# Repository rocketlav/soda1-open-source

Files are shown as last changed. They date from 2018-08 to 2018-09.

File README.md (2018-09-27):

# SODA1 Open source rocket project
SODA1 открытый проект одноступенчатой экспериментальной ракеты для вывода атмосферного зонда CanSat в рамках чемпионата RosCanSat 2018. Проект разработан участниками студенческого конструкторского бюро "RocketLAV" Самарского университета, занявших первое место на этом чемпионате. Здесь мы собрали всю документацию, включая чертежи, которые разрабатывали и использовали во время создания данной экспериментальной ракеты. Мы хотим поделиться со всеми желающими и интересующимися нашими знаниями и опытом, надеемся, что вы сможете использовать наши результаты для изучения программирования, электроники и механики. 
***

rocket
rocket

***

Проектные файлы хранятся в четырех папках:
1. В папке Documentation содержится PDF файл с подробным описанием проекта;
2. В папке Electrical разводка платы электроники и ее принципиальная схема, а также исходник для altium designer;
3. В папке Mechanical содержатся чертежи, 3D модели в формате STL и исходники 3D модели Kompas v17;
4. В папке Software содержатся исходный код для платы электроники и алгоритм ее работы.

***

Для того, чтобы скачать весь проект, нажмите на зеленую кнопку "Clone or download" и выберите "Download ZIP".

Если у вас возникли вопросы в процессе работы или у вас есть для нас предложение, пожалуйста, напишите нам на почту: rocketlav.team@gmail.com

или используйте сообщения нашей группы https://vk.com/rocketlav.

# English version

SODA1 is open source project of experimental single stage rocket which is designed to deliver CanSat during Russian CanSat competition 2018. This project was designed by members of student design association "RocketLAV", which won the first prize of this competition. Our team collect all documentation here which we developed and used during rocket's creation. We want to share our knowledge and experience for those who want and interested in it, we hope that you can use our documentation to get learned in software, electronics and mechanical engineering. 

***

Project documentation are placed in four folders:
1. Main PDF file which describes project in detail is placed in Documentation folder, please, be attention, this file fully in Russian;
2. PCB files of electrical board and its principal scheme are placed in Electrical folder; 
3. Mechanical folder contains drawings and 3D model of rocket in stl format and Kompas v17;
4. Software folders contains a source code and algorithms for electrical board of rocket.

***

Mostly this project in russian, but if you need help to translate, feel free to contact us.
If you have any questions about our project or you have an offer for us, please, write to us on email rocketlav.team@gmail.com.

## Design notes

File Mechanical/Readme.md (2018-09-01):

# Описание файлов
Здесь содержатся чертежи в папке Drawings, по которым вы можете изготовить модель ракеты. 

В папке 3D Model содержатся исходники модели и ее сборка, выполенная в среде Компас v17. Также в папках Head Fairings V1 и Head Fairings V2 содержатся 3д модели вариантов механизма открытия головного обтекателя. 

Файлы В разрезе.stl и Без разреза.stl 3д модель ракеты соответственно в разрезе и без разреза в формате STL.

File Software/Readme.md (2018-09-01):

# Описание файлов

EOS_code.ino исходные код для платы бортовой системы. Пины актуальны для разведенной платы, представленной в папке Electrical. 
Если вы собираетесь использовать протокол i2c для подключения барометра, пожалуйста, проверьте адресс устройства через i2c scan. Скетч i2c scan вы можете найти на оффициальном сайте arduino. Полученный адрес вашего устройства необходимо добавить в библиотеку <Adafruit_BMP280.h> для правильной работы барометра.

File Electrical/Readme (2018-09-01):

Описание файлов:

Onboard+Plate+ver1 (altium designer.).pcbdoc исходник платы в altium designer.

PCB Lower Layer.pdf и PCB Upper Layer.pdf разводка платы для ее изготовления методом ЛУТ. PCB_Onboard-Plate.pdf - изображение разводки платы со всеми слоями. Schematic_SODA1_OnBoardElectricalSystem.pdf - принципиальная электроическая схема. 

Это наш первый опыт в разработке и создании плат, по этому мы рекомендуем развести эту плату самостоятельно. Так как плата двухсторонняя, компоненты платы размещается так, чтобы было удобно их паять.

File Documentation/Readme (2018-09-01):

SODA1_Project_Documentation.pdf файл с подробным описанием проекта. В нем содержатся технические подробности, обоснования принятых решений, а также расчеты, которые проводились во время создания проекта.

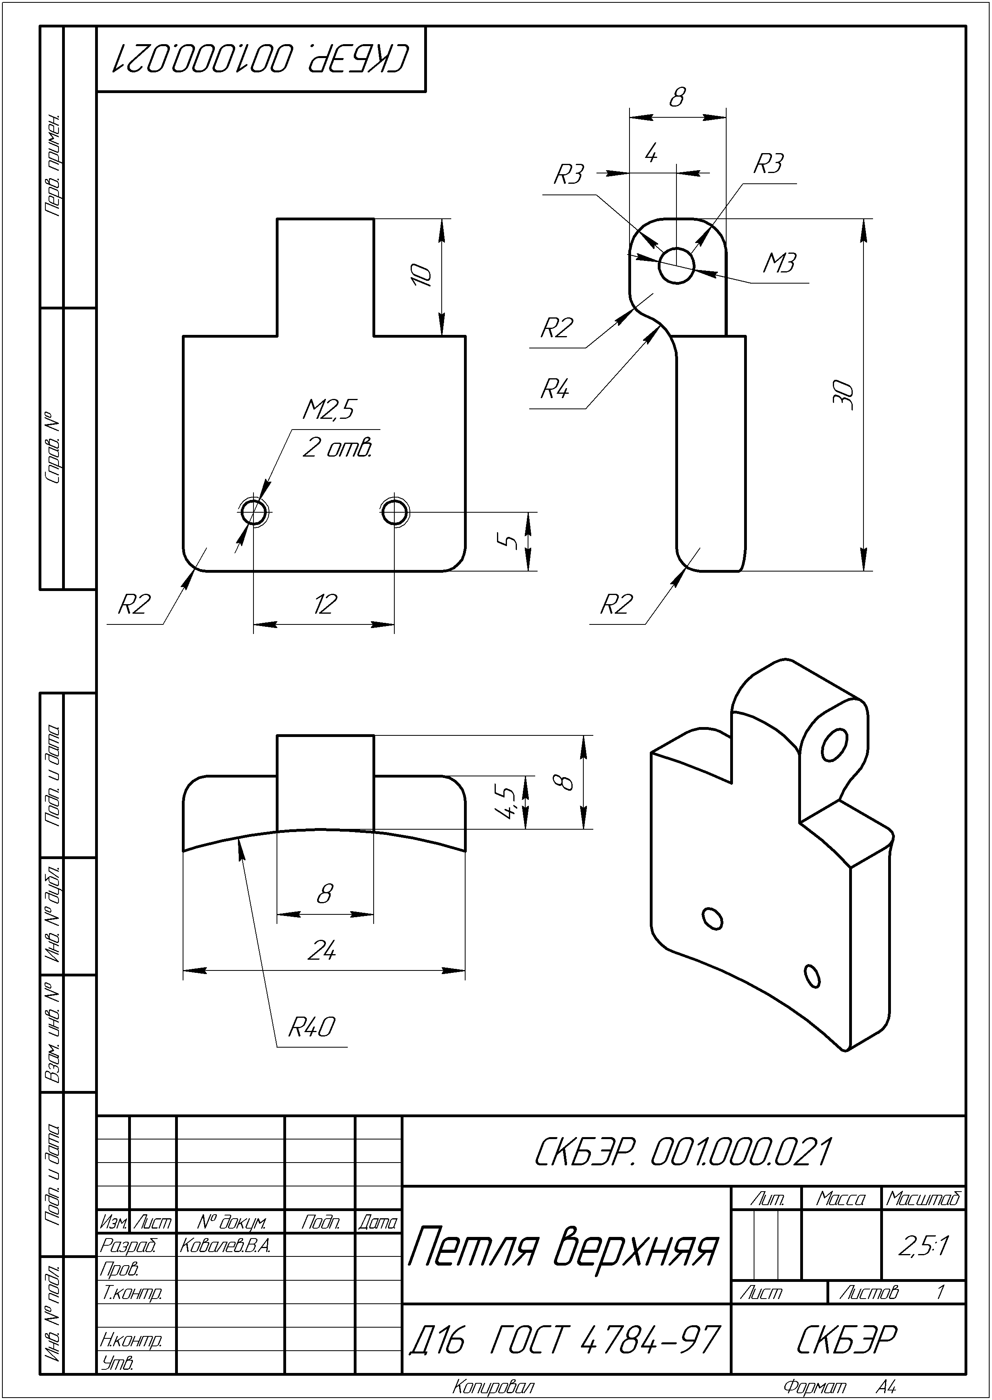
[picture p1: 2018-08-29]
Mechanical/Drawings/21Петля верхняя.png

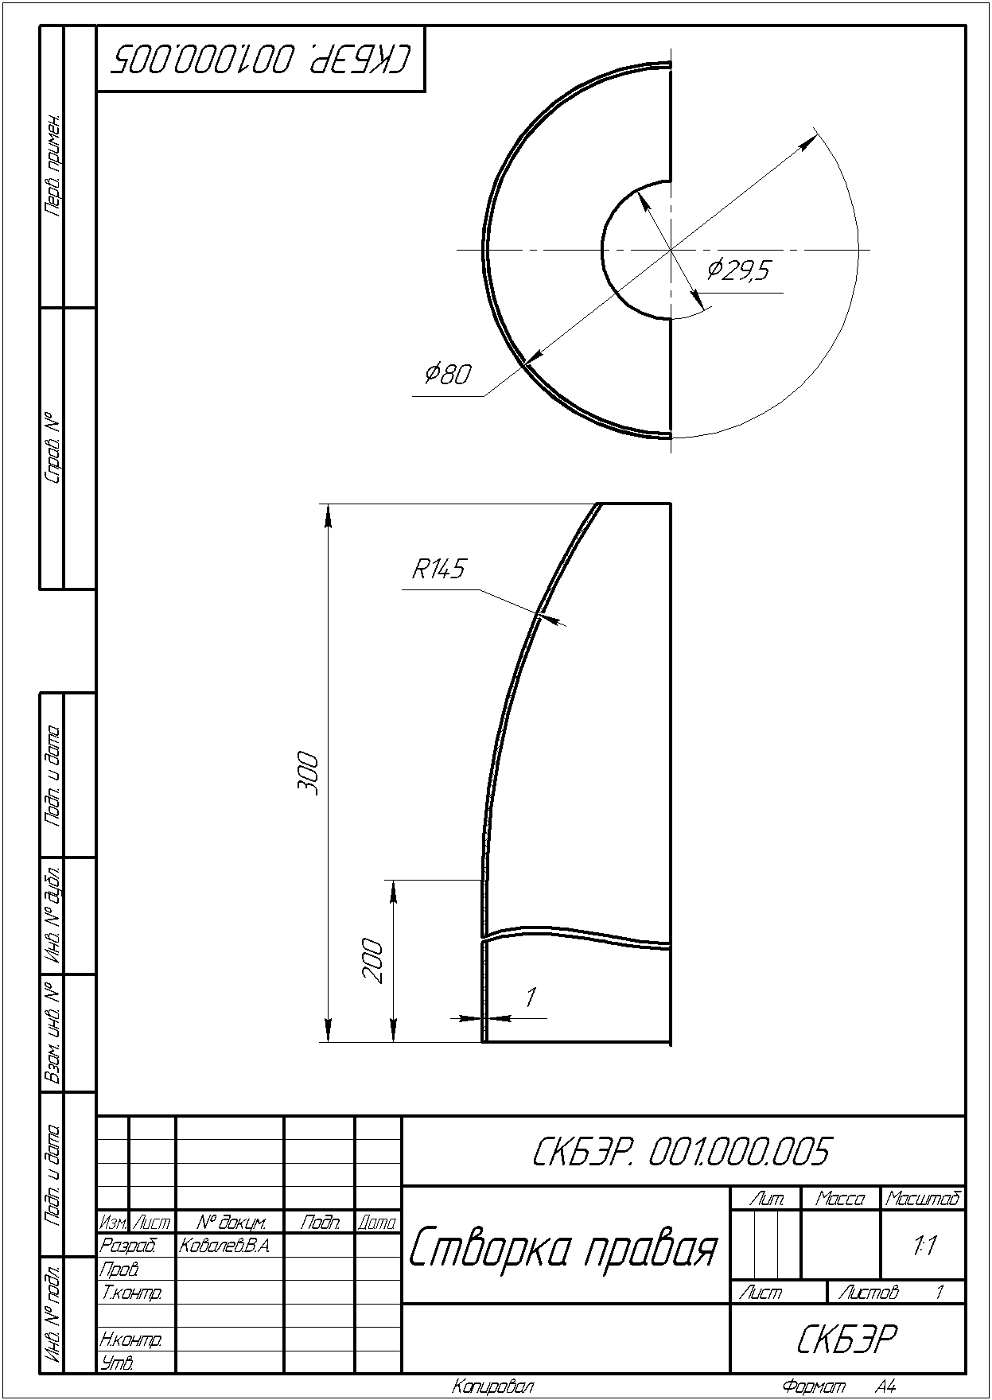
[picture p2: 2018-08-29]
Mechanical/Drawings/5Створка правая.png

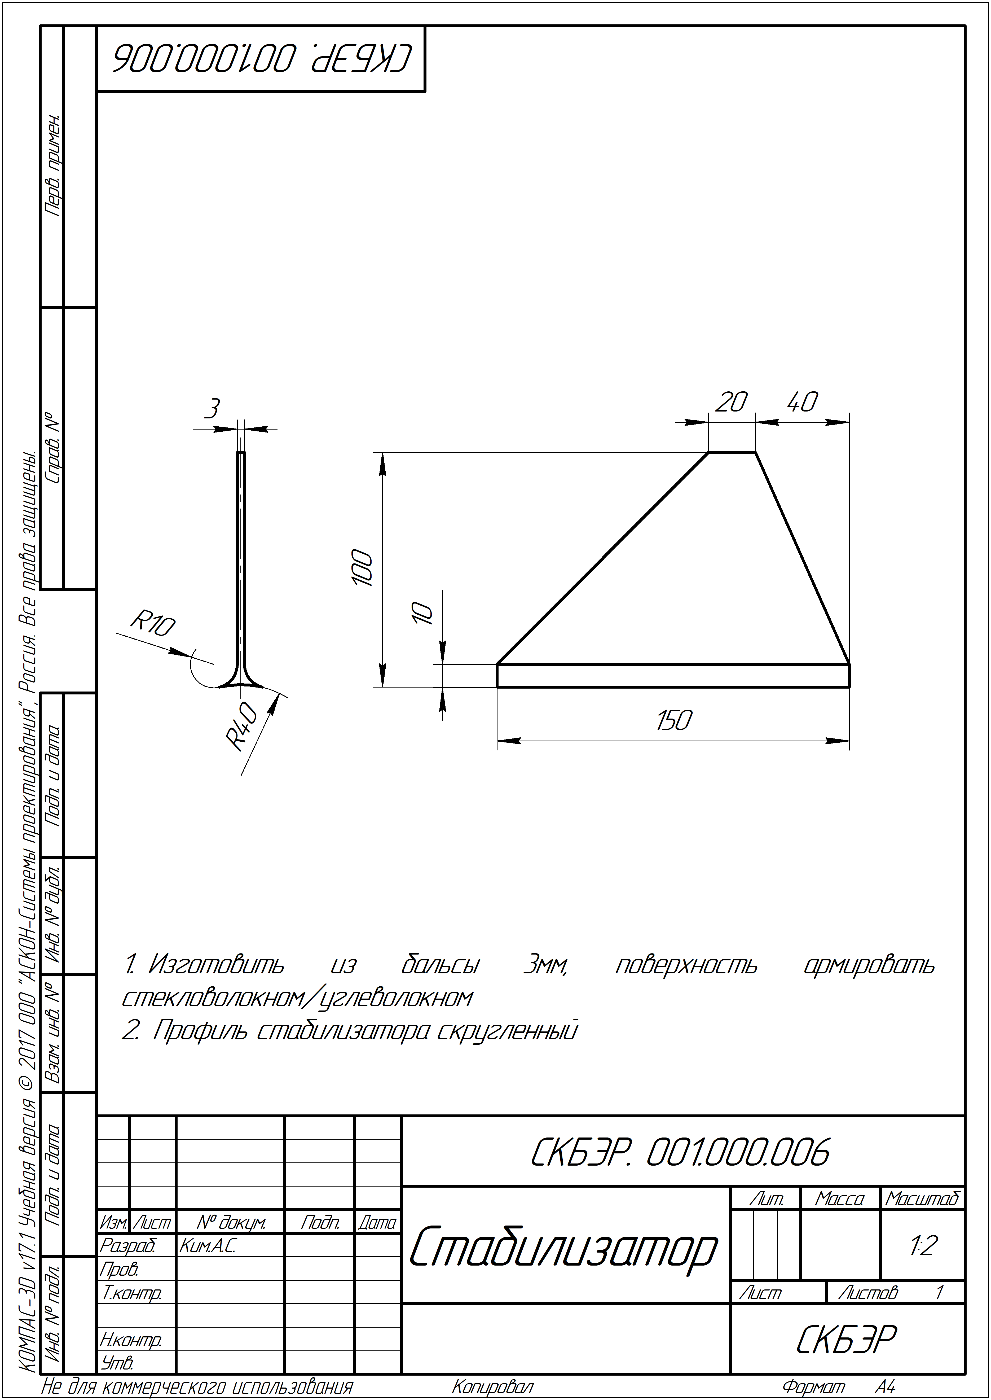
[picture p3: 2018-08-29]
Mechanical/Drawings/6Стабилизатор .png

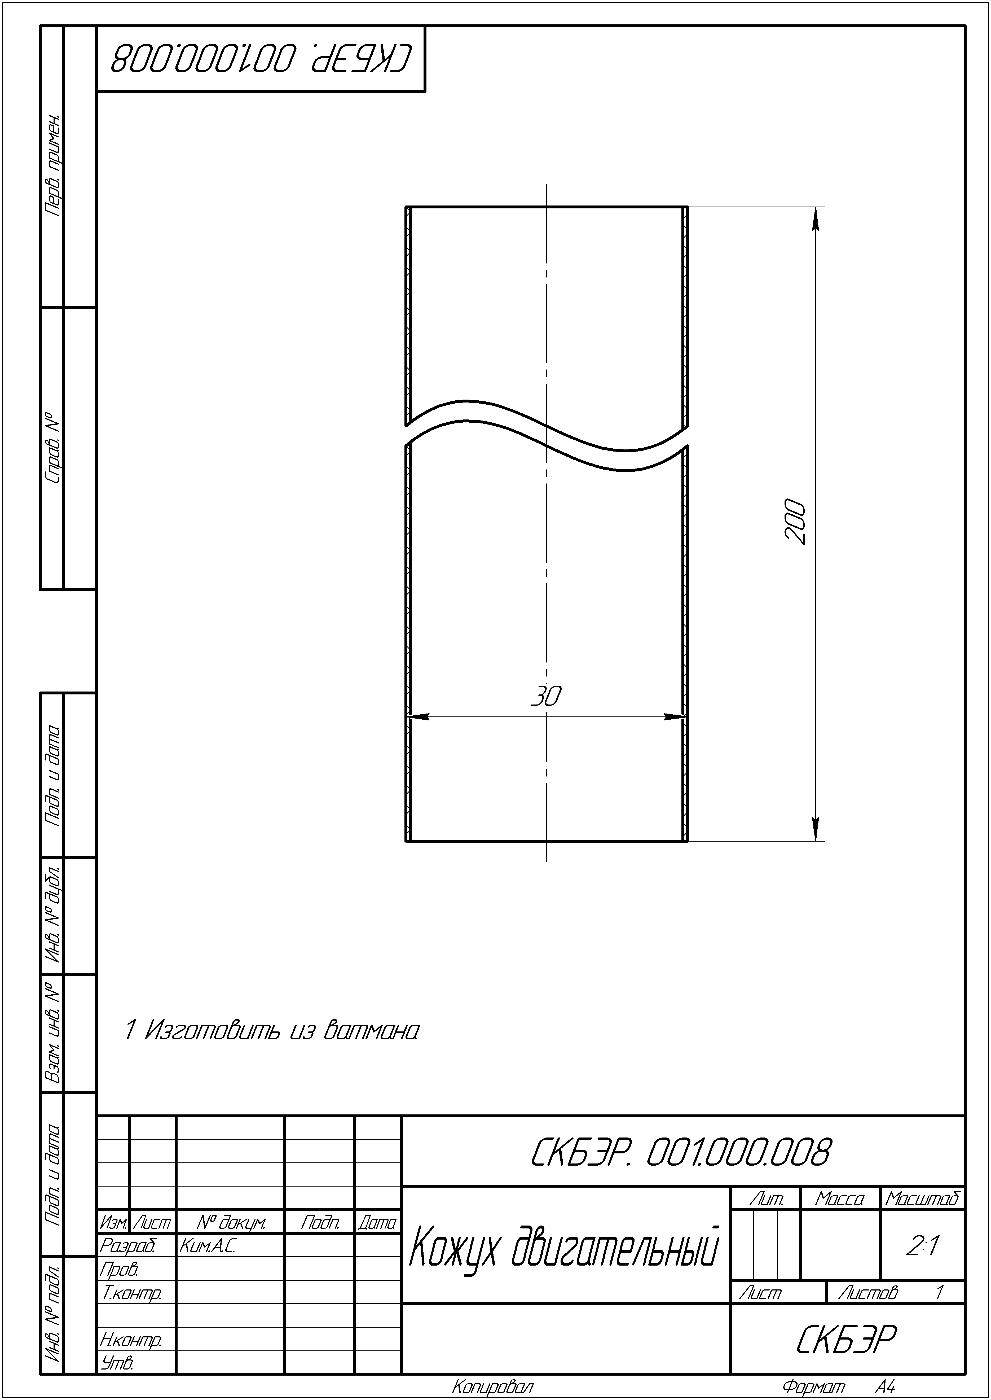
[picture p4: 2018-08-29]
Mechanical/Drawings/8Кожух двигательный.png

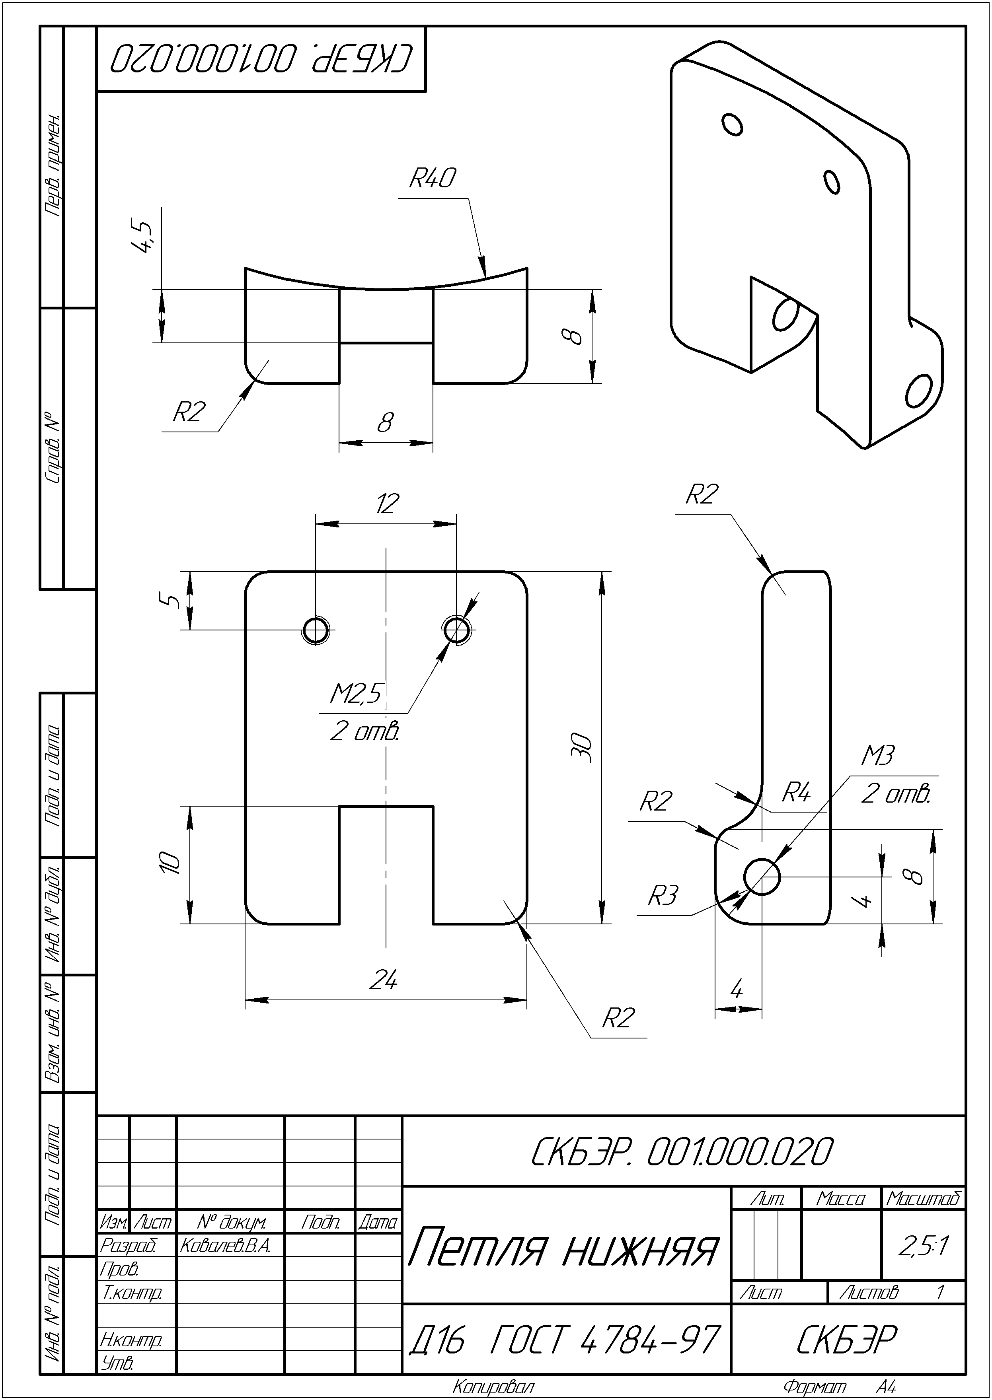
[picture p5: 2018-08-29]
Mechanical/Drawings/20Петля нижния.png

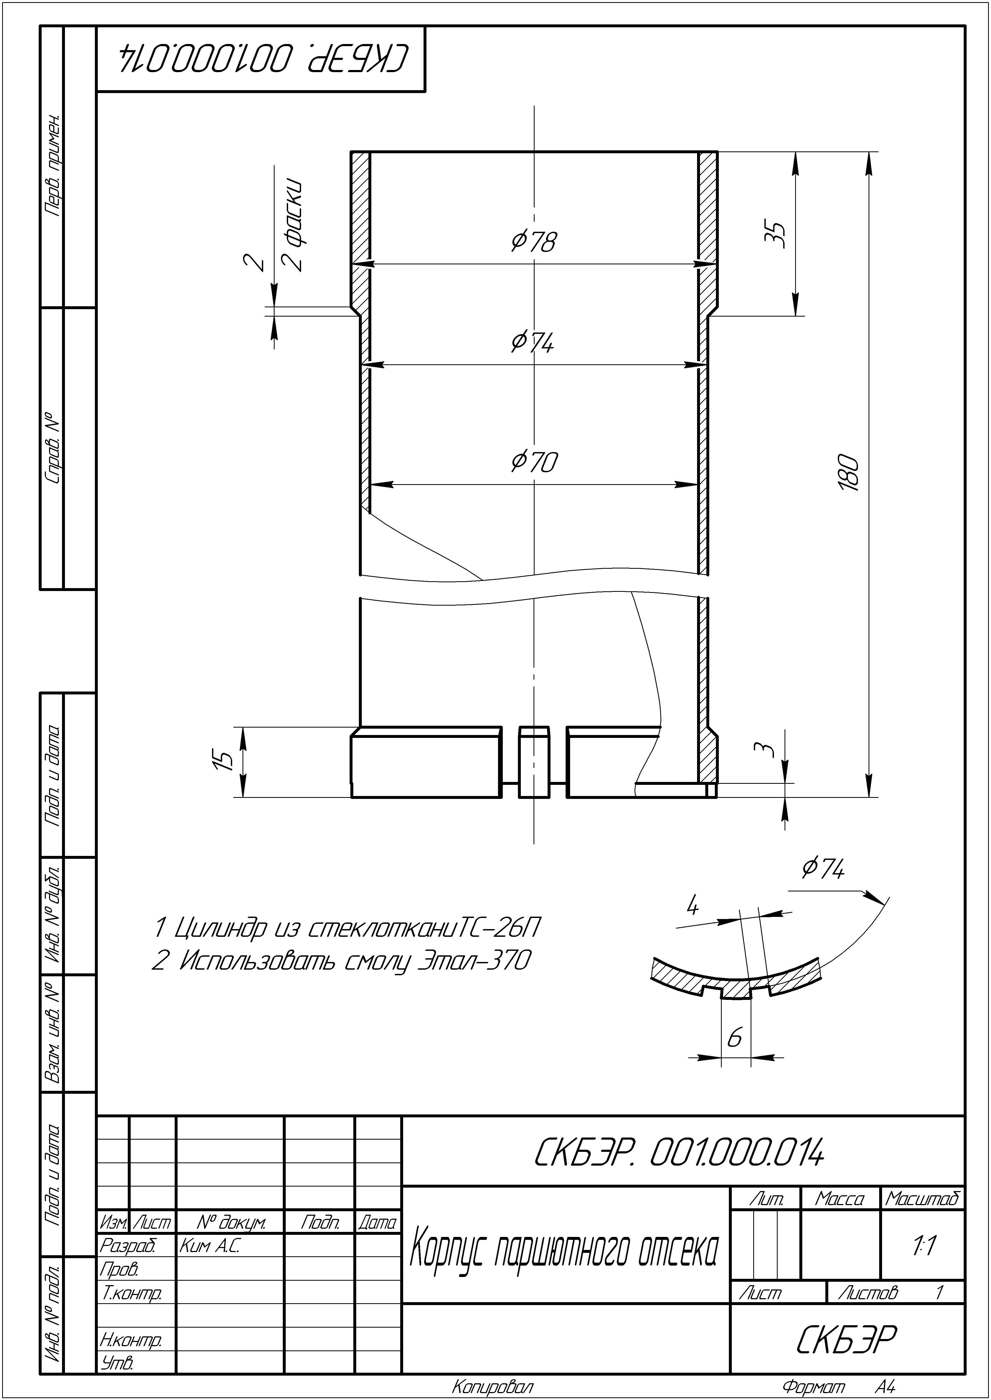
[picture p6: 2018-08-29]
Mechanical/Drawings/14Корпус парашютного отсека.png

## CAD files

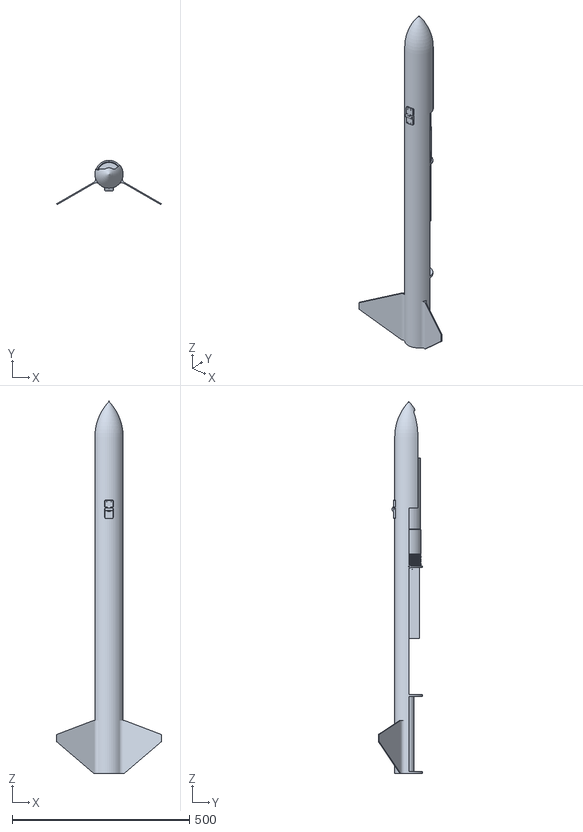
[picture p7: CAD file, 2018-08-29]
Mechanical/В разрезе.stl
295.9 x 125.3 x 1050.0

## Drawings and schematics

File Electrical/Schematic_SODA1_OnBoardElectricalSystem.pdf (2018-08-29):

## Power supply

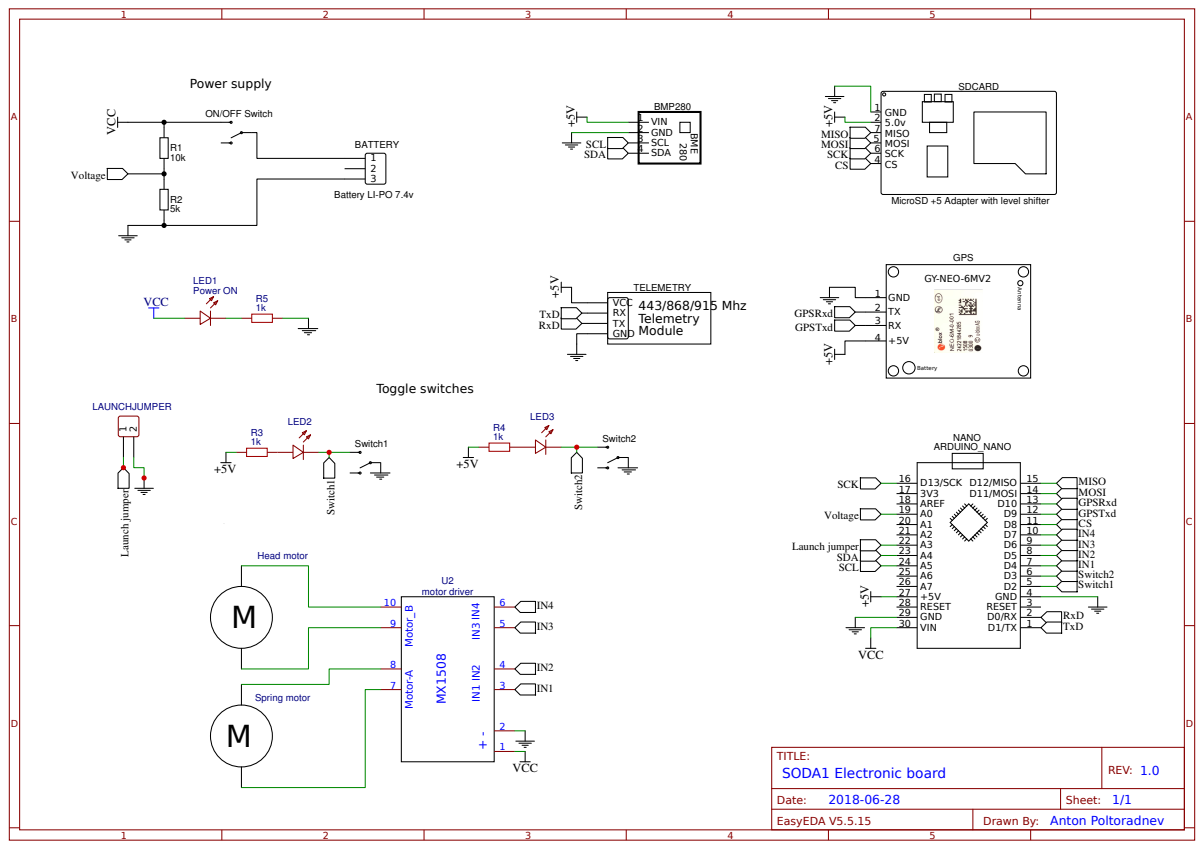
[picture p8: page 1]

MicroSD +5 Adapter with level shifter

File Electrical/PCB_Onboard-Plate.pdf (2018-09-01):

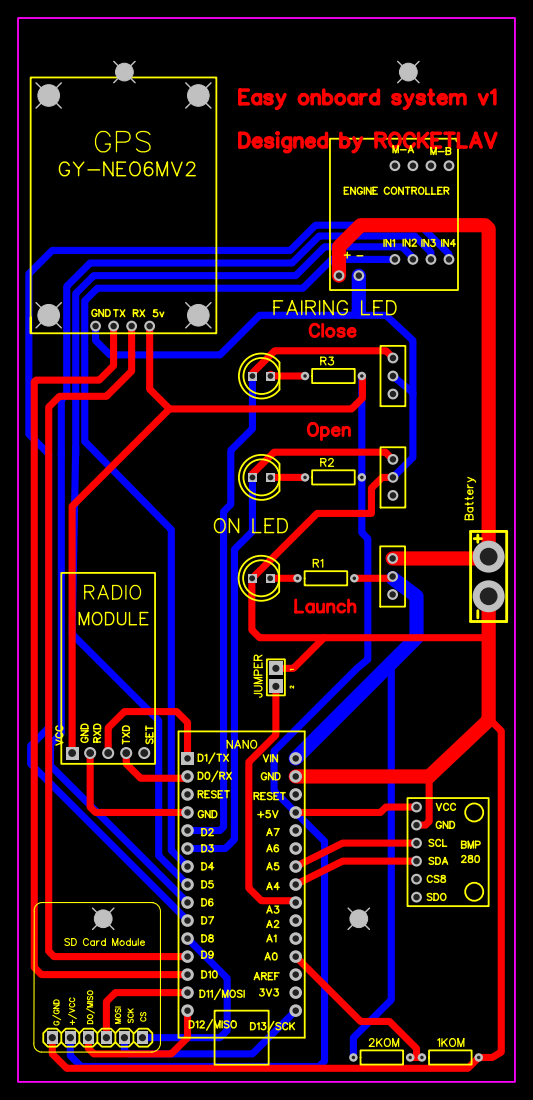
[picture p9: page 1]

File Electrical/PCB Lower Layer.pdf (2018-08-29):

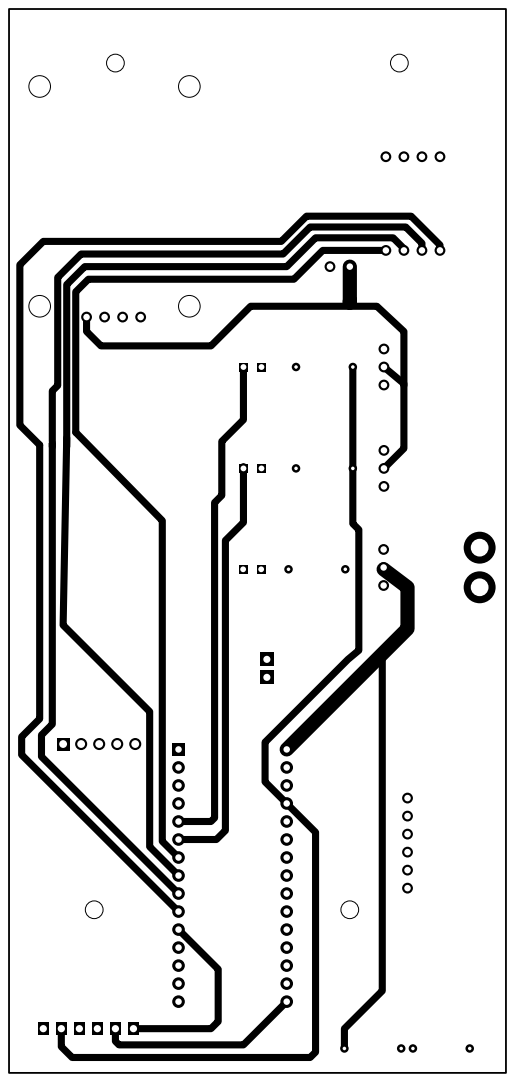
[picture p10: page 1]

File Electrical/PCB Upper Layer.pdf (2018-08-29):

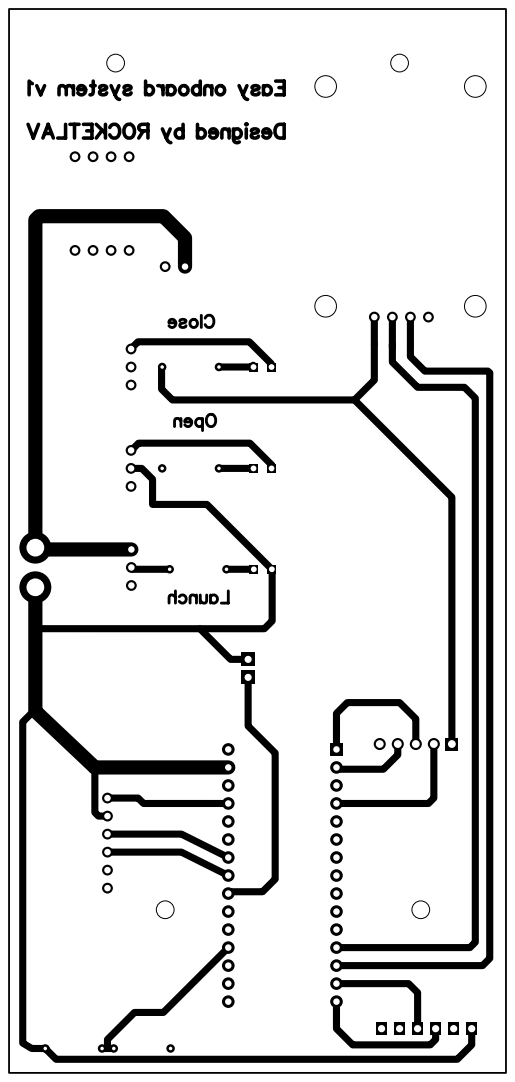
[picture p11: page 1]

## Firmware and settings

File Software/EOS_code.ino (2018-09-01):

#include <Adafruit_BMP280.h> // Изменить в этой бибилотеке адрес устройства на 0x76
#include <SoftwareSerial.h>
#include <SD.h>

/// Контактные пины, не трогать, в плате они фиксированные
SoftwareSerial GPS(9, 10); //Инициализация GPS по программному сериалу RX, TX
Adafruit_BMP280 BMP;   //Инициализация барометра
const int chipSelect = 8; //Тоже фиксированный пин на плате
File dataFile;

// ПЕРЕМЕННЫЕ

unsigned long DelayForBMP = 125; // Время опроса барометра
unsigned long BufferForBMP = 0;

unsigned long DelayForSD = 10000; // Время сохранения данных на сд
unsigned long BufferForSD = 0;

float BMSKoef = 0.01346; //Коэффициент для определения напряжение на аккумуляторе, для вашего аккума нужно рассчитать самостоятельно

unsigned long StartTime = 0;
unsigned long SaveTimer = 5500; // Время раскрытия после отрыва
unsigned long SaveEndTime = 1500; // Время работы двигателя системы открытия
unsigned long EndBuffer = 0;

unsigned long Save2Timer = 1000; // + SaveTimer система спасения
unsigned long Save2EndTime = 1500; // Время работы двигателя системы открытия
unsigned long End2Buffer = 0;

bool StartDrive = false;
bool Start2Drive = false;

void setup()
{
  pinMode(A0, INPUT); // VCC VOlTAGE
  pinMode(A3, INPUT_PULLUP); // jumper
  pinMode(3, INPUT); // пружина (Верхний)
  pinMode(2, INPUT); // голова (Нижний)
  // motor
  pinMode(4, OUTPUT); // Пружина
  pinMode(5, OUTPUT);

  pinMode(6, OUTPUT); // Голова
  pinMode(7, OUTPUT);

  // Инициализация всех портов
  Serial.begin(9600); // БОД радио модуля
  while (!Serial) {
    // wait for serial port to connect. Needed for native USB port only
  }

  GPS.begin(9600);

  if (!BMP.begin()) {  //Подключаем барометр
    Serial.println("BMP NOT FOUND");
  }
  else Serial.println("BMP IS OK");

  if (!SD.begin(chipSelect)) {
    Serial.println("Card failed, or not present");
  }
  else Serial.println("CARD IS OK");

  dataFile = SD.open("datalog.txt", FILE_WRITE);

  float voltage = analogRead(A0) * BMSKoef;
  Serial.println("Voltage: " + String(voltage));
  dataFile.println("Voltage: " + String(voltage));

  Serial.println("GPS value: ");
  // GPS tester
  bool gpsTester = false;
  while (!gpsTester) {
    while (GPS.available()) {
      char a = GPS.read();
      Serial.write(a); // Вывод в радио
      gpsTester = true;
    }
  }

  Serial.println("");
  Serial.println("INIT END");

  bool isReady = false;
  int headValue = digitalRead(2);
  int springValue = digitalRead(3);
  bool ok = true;
  while (!isReady) {
    if (headValue == 0 && springValue == 0 && ok) {
      Serial.println("READY FOR START, WAITING FOR A JUMPER UNLOCK");
      ok = false;
    }
    if (headValue == 0 && springValue == 0) {
      while (GPS.available()) {
        char a = GPS.read();
        dataFile.write(a);
        Serial.write(a); // Вывод в радио
      }
    }
    if (digitalRead(A3) == 1) {
      isReady = true;
      Serial.println("START");
    }



    int head = digitalRead(2);
    if (head != headValue) {
      if (head == 1) {
        headValue = 1;



        Serial.println("SPRING IS OPENNING");
        digitalWrite(4, HIGH);
        digitalWrite(5, LOW);
        delay(SaveEndTime * 2);
        digitalWrite(4, LOW);
        digitalWrite(5, LOW);
        Serial.println("SPRING OPENED");

      }
      else {
        headValue = 0;
        Serial.println("SPRING IS CLOSING");
        digitalWrite(4, LOW);
        digitalWrite(5, HIGH);
        delay(SaveEndTime);
        digitalWrite(4, LOW);
        digitalWrite(5, LOW);
        Serial.println("SPRING CLOSED");
        ok = true;
      }
    }

    int spring = digitalRead(3);
    if (spring != springValue) {
      if (spring == 1) {
        springValue = 1;

        Serial.println("HEAD IS OPENNING");
        digitalWrite(6, HIGH);
        digitalWrite(7, LOW);
        delay(Save2EndTime * 2);
        digitalWrite(6, LOW);
        digitalWrite(7, LOW);
        Serial.println("HEAD OPENED");
      }
      else {
        springValue = 0;
        Serial.println("HEAD IS CLOSING");
        digitalWrite(6, LOW);
        digitalWrite(7, HIGH);
        delay(Save2EndTime);
        digitalWrite(6, LOW);
        digitalWrite(7, LOW);
        Serial.println("HEAD CLOSED");
        ok = true;
      }
    }
  }
  StartTime = millis();
}

void loop()
{
  // BMP280
  if (millis() - BufferForBMP > DelayForBMP) {
    float info = BMP.readAltitude(1013.25);
    dataFile.println("<MILLIS : " + String(millis() - StartTime) + " BMP : " + String(info) + ">");
    //Serial.println("MILLIS : " + String(millis() - StartTime) + " BMP : " + String(info));
    BufferForBMP = millis();
  }

  // GPS
  while (GPS.available()) {
    char a = GPS.read();
    dataFile.write(a);
    Serial.write(a); // Вывод в радио
  }

  if (millis() - BufferForSD > DelayForSD) {
    if (dataFile) dataFile.close();
    dataFile = SD.open("datalog.txt", FILE_WRITE);

    BufferForSD = millis();
  }

  if (!StartDrive && millis() - StartTime > SaveTimer) {
    StartDrive = true;
    EndBuffer = millis();
    digitalWrite(6, HIGH);
    digitalWrite(7, LOW);
  }
  if (!Start2Drive && millis() - StartTime > SaveTimer + Save2Timer) {
    Start2Drive = true;
    End2Buffer = millis();
    digitalWrite(4, HIGH);
    digitalWrite(5, LOW);
  }
  if (millis() - EndBuffer > SaveEndTime * 2) {
    digitalWrite(6, LOW);
    digitalWrite(7, LOW);
  }
  if (millis() - End2Buffer > Save2EndTime * 2) {
    digitalWrite(4, LOW);
    digitalWrite(5, LOW);
  }

}
